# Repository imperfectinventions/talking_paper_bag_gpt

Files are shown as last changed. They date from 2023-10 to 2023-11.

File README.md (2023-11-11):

# Talking Paper Bag GPT

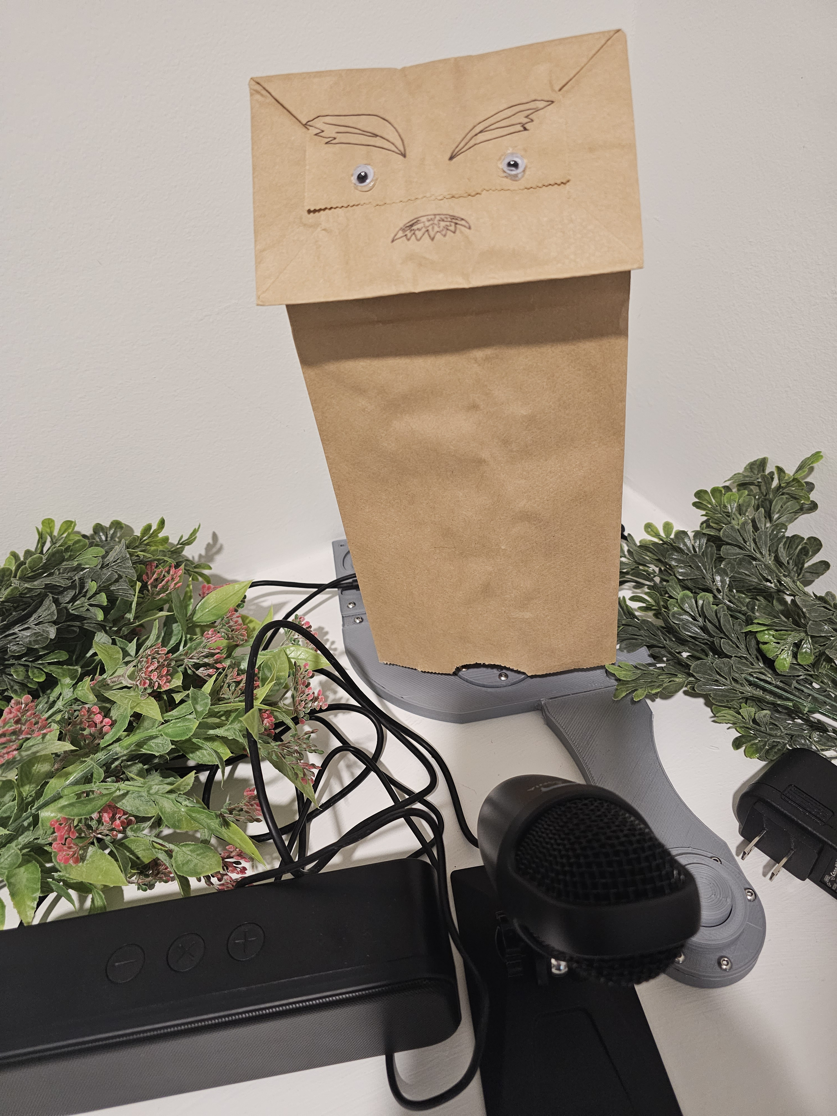
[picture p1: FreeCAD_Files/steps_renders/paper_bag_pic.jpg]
Paper Bag Image


[Demo Link](https://www.instagram.com/p/CzWKE8drE5b/)

# Table of Contents
- [Introduction](#introduction)
- [Requirements](#requirements)
   - [Bill of Materials](#bill-of-materials)
   - [Tools Needed](#tools-needed)
- [Assembly](#assembly)
   - [Print Settings](#print-settings)
   - [Assembly and Setup Steps](#assembly-and-setup-steps)

## Introduction

This device turns any paper bag into a talking puppet! It uses OpenAI's GPT3.5 turbo as well as the Azure Speech service in order to enable communication with this paper bag.

You can also give the paper bag a personality via specifying the system message. I have a few pre-built personalities that you can use (a lot of them are problematic, though so heads up).

## Requirements

### Bill of Materials

|  Name | Purpose | Amazon Link |
|---|---|---|
| 1 Libre AML-S905X-CC | The Brains of the system. Can run linux. Future updates may involve using MicroPython and remove the need for an OS, but this is the current design. Also has 4 USB ports, so it was easy to run USB peripherals on them. | [link](https://www.amazon.com/gp/product/B074P6BNGZ/ref=ppx_yo_dt_b_search_asin_title?ie=UTF8&th=1) |
| 1 SD Card | This will be the non-volatile storage | [link](https://www.amazon.com/SanDisk-Extreme-microSDXC-Memory-Adapter/dp/B09X7BK27V/ref=sr_1_6?keywords=sd+card) |
| 1 Wifi Dongle | WiFi connectivity. This board does have an Ethernet plug so you can use that and free up a USB port. I just went with this. | [link](https://www.amazon.com/gp/product/B0BNFKJPXS/ref=ppx_yo_dt_b_search_asin_title?ie=UTF8&psc=1) |
| Some Stranded Wire | To connect everything together | [Link to the Wire I Used](https://www.amazon.com/gp/product/B077HQ779B/ref=ppx_yo_dt_b_search_asin_title?ie=UTF8&psc=1) |
| Crimp Connectors | To make the wire connections. You could bring your own pre-made wires for this, but I just decided at one point it was cheaper to make my own. | [Link with Crimper](https://www.amazon.com/gp/product/B07VQ6YNSC/ref=ppx_yo_dt_b_search_asin_title?ie=UTF8&psc=1) |
| 1 SG90 Servo | To move the paper bag head. | [Link](https://www.amazon.com/gp/product/B07Q6JGWNV/ref=ppx_yo_dt_b_search_asin_title?ie=UTF8&psc=1) |
| Hot Glue | For glueing things together when needed | [Link](https://www.amazon.com/AdTech-Glue-Sticks-Full-Clear/dp/B000PCY91O/ref=sr_1_4?keywords=glue+gun+sticks) |
| M3 Screws of Various Sizes | For securing all of the 3D printed parts together | [Link](https://www.amazon.com/gp/product/B08H24W42K/ref=ppx_yo_dt_b_search_asin_title?ie=UTF8&psc=1) |
| A USB Speaker | For hearing ChatGPT talk to you. Could go with a combined speaker/microphone.  | [Link](https://www.amazon.com/gp/product/B08QRYTPGH/ref=ppx_yo_dt_b_search_asin_title?ie=UTF8&psc=1) |
| A USB Microphone | For talking to ChatGPT. Could go with a combined speaker/mic. Similar to the one I used. | [Link](https://www.amazon.com/Cyber-Acoustics-Premium-Condenser-Microphone/dp/B0857HD2PT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) |
| PLA Filament | For making the full 3D-printed assembly. | [Link](https://www.amazon.com/gp/product/B08QN5FQX7/ref=ppx_yo_dt_b_search_asin_title?ie=UTF8&psc=1) |
| Some solid core wire | For the button | [Link](https://www.amazon.com/gp/product/B081GMJVPB/ref=ppx_yo_dt_b_search_asin_title?ie=UTF8&psc=1) |
| A Push Button | For controlling when to talk to the Paper Bag | [Link](https://www.amazon.com/gp/product/B09R47N37H/ref=ppx_yo_dt_b_search_asin_title?ie=UTF8&psc=1) |
| Paper Bags | For the whole aesthetic |  | 
| Paper Bag Decorations | For decorations |  |

### Tools Needed

|  Name | Purpose | Amazon Link |
|---|---|---|
| Wire Stripper | Stripping Wires | [Link](https://www.amazon.com/gp/product/B09539R6TD/ref=ppx_yo_dt_b_search_asin_title?ie=UTF8&psc=1) |
| 3D Printer | For printing the full 3D printer assembly | [I use a modded Geeetech A10, but link to some random printer](https://www.amazon.com/Comgrow-Creality-Ender-Aluminum-220x220x250mm/dp/B07BR3F9N6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) | 
| Soldering Iron | For soldering | [Link to Default Soldering Iron, not sponsored](https://www.amazon.com/Soldering-Digital-Welding-Portable-Electric/dp/B08R3515SF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) |
| Hot Glue Gun | For some touch up jobs, securing wires in place, etc. | |

## Assembly

### Print Settings

I printed most parts with 15% infill and surrounded the screw holes and some weak points with 90% infill using a support block in Cura.

### Assembly and Setup Steps

#### Step 1

Step 1

#### Step 2

Step 2

#### Step 3

Step 3

#### Step 4

Step 4

#### Step 5

Step 5

#### Step 6

Step 6

#### Step 7

Step 7

#### Step 8

Step 8

#### Step 9

Step 9

#### Step 10

Step 10

#### Step 11a

Step 11a

#### Step 11b

Step 11b

#### Step 12

Step 12

#### Step 13

Step 13

#### Step 14a

Step 14a

#### Step 14b

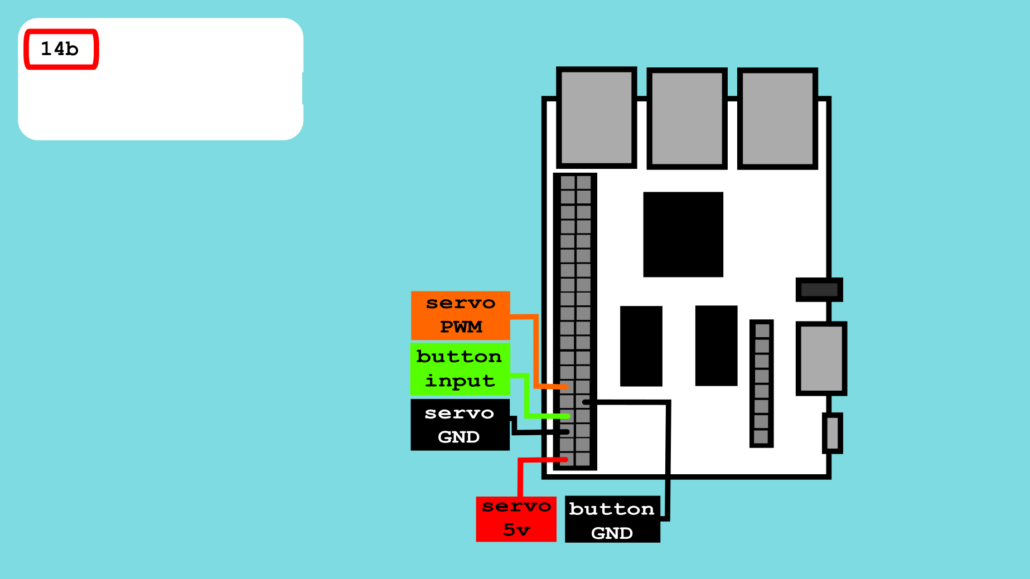
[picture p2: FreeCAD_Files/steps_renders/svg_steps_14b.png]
Step 14b


#### Step 15a

Step 15a

#### Step 15b

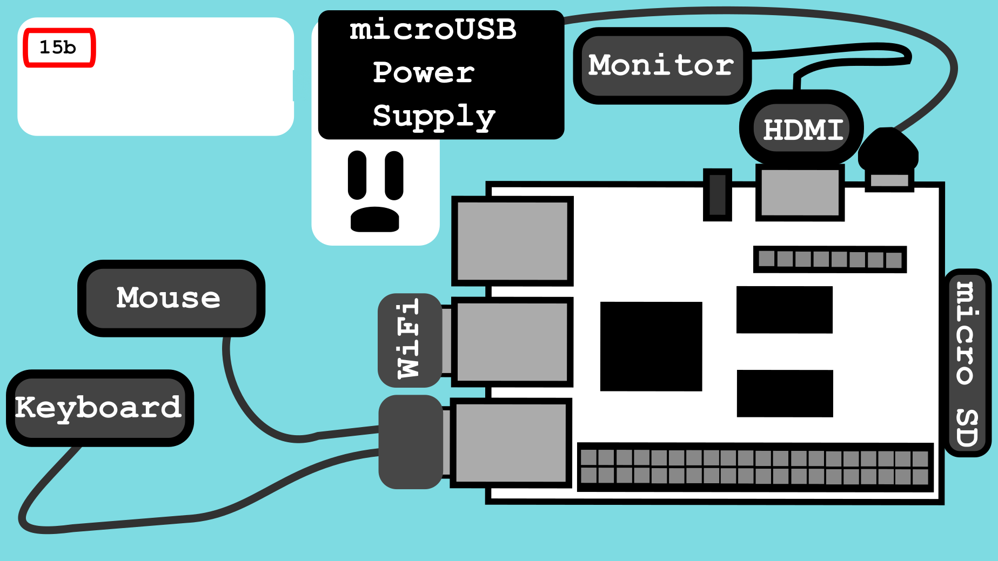
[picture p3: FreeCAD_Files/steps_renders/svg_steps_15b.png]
Step 15b


#### Step 15c: Install the OS

You will now need to set up your micro SD card to hold the OS (or if you go with an eMMC, go with that). The steps for installing Raspbian onto the micro SD is [here](https://hub.libre.computer/t/raspbian-11-bullseye-for-libre-computer-boards/82).

After you install the OS, insert the micro SD into the micro SD slot (shown in step 15a). 

#### Step 15d: Set up your SSH host 

Now that you have a user account set up, make sure to set up your SSH host (just so that you don't need to have a keyboard, mouse, and monitor plugged into the Libre Computer so you can plug in your other devices. NOTE this is only needed if using USB for everything. If you use AV, then you don't necessarily have to do this step).

```bash
sudo apt install openssh-server openssh-client
```

[Reference](https://www.tecmint.com/install-openssh-server-in-linux/)

#### Step 15e: Make sure the Latest Version of Python is Installed

[Follow These Instructions](https://raspberrytips.com/install-latest-python-raspberry-pi/)

#### Step 15f: Install the Necessary Pip Packages (no dokerfile)

If using the dockerfile, skip to [Step 16](#step-16) (recommended you use docker). Follow all the steps normally, then do [Step 22: Docker](#step-22-docker)

With venv
```bash
sudo apt-get install python3-libgpiod #for the gpiod library

python3 -m pip install virtualenv --system-site-packages
python3 -m pip venv pbg-venv
source pbg-venv
pip install -r requirements.txt
```
Witout venv
```bash
pip install -r requirements.txt
```

#### Step 16

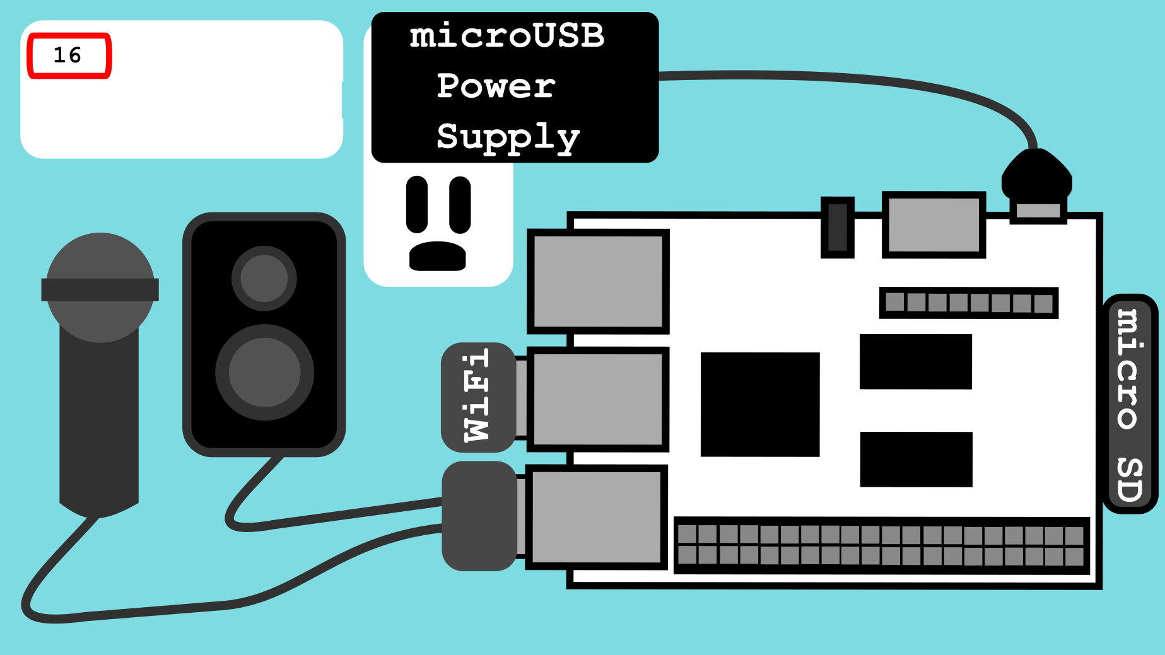
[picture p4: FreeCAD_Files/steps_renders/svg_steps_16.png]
Step 16


#### Step 17: Clone this repo

Clone this repo onto the Libre computer. If you have done this already, kudos. If you have not, do it now.

#### Step 18: Create the cloud resources

[Create a Microsoft Azure Account](https://azure.microsoft.com/en-us/free/)

[Create an Azure subscription or Use an Existing One](https://learn.microsoft.com/en-us/azure/cost-management-billing/manage/create-subscription)
[How to Install and Configure Terraorm for Microsoft Azure](https://learn.microsoft.com/en-us/azure/developer/terraform/quickstart-configure)

Once there is an Azure subscription, terraform is set up, and "az login" or the equivalent command has been run, then it's time to set up the resource groups and the speech/other resources needed.
```bash
#for creating the service account used (make sure to get the account information from this)
cd terraform_code/accounts
terraform init
terraform apply
#for the resource group
cd terraform_code/resource_group
terraform init
terraform apply
```
Then update the settings.yaml file (in the terraform_code directory) with your desired allowed IP addresses that should access your key vault (needs to be the public IP(s) that the Libre Computer is going to connect to). Specify the CIDR and the IP address.

```bash
#for the actual azure resources
cd terraform_code/speech2text
#this terraform will use the settings.yaml file.
terraform init
terraform apply
```

Verify the resources exist:
Look under "resource groups" on portal.azure.com and find the correct resource group known as rg-sbt-ai. Then click on it and make sure the speech resource and the key vault are there
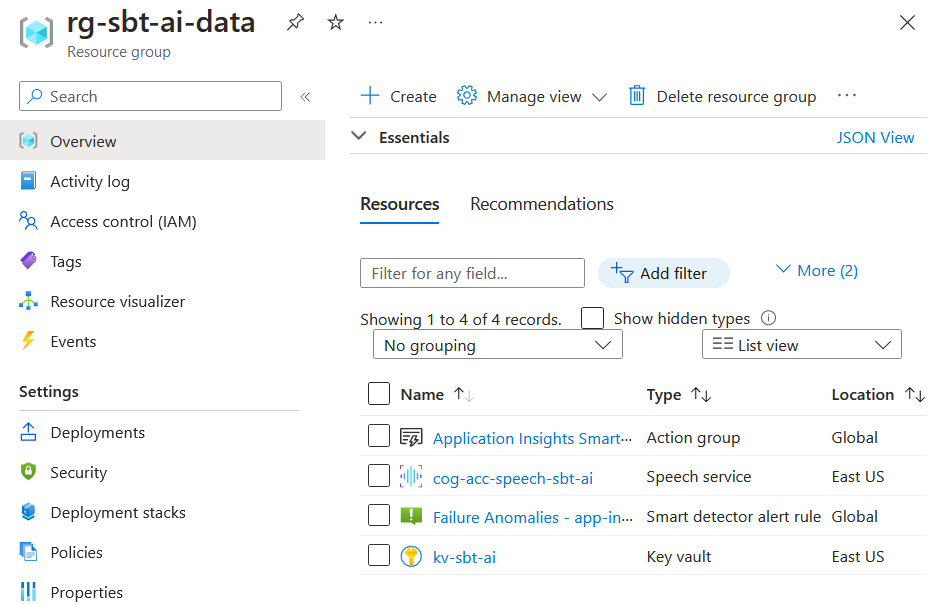
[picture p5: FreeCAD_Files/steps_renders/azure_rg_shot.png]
Look under "resource groups" on portal.azure.com and find the correct resource group known as rg-sbt-ai. Then click on it and make sure the speech resource and the key vault are there


#### Step 19: Get the Azure speech API key

Go to the Azure speech resource named cog-acc-speech-sbt-ai and go down to where it says "KEYS". Use any one of those keys
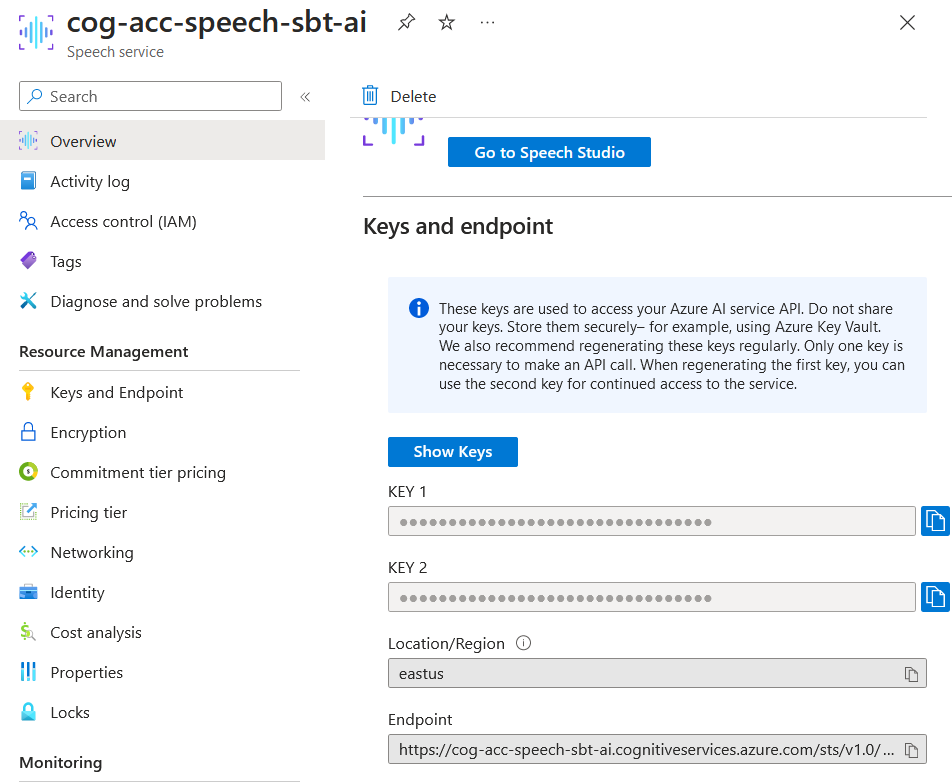
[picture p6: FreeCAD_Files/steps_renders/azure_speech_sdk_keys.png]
Go to the Azure speech resource named cog-acc-speech-sbt-ai and go down to where it says "KEYS". Use any one of those keys


#### Step 20: Get the OpenAI API key

Now got and set up an account with OpenAI. Once done, go to "View API Keys" and "Create a new secret key". This is the key that you will use in step 20 when inserting it into the settings.py file.

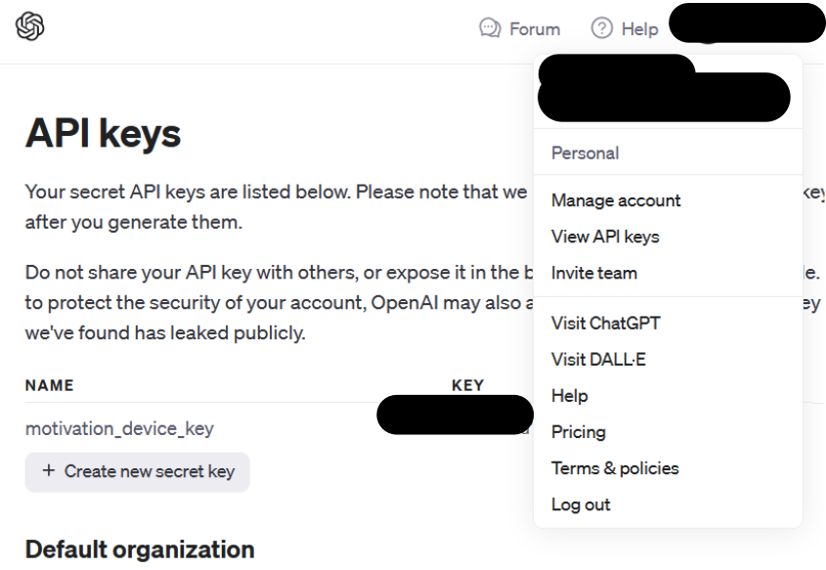
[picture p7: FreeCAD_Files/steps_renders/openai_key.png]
Now got and set up an account with OpenAI. Once done, go to "View API Keys" and "Create a new secret key". This is the key that you will use in step 20 when inserting it into the settings.py file


#### Step 21: Define the settings file

On the Libre Computer clone of this repo in the file named "settings.py", fill out your values. Each value in the settings.py has an explanation where to pull each value from.

#### Step 22: Run it on the Libre Computer! (no docker)

```bash
python main.py
```

#### Step 22: Docker

If running in docker, then:

```bash
#go into the cloned repo's code where the dockerfile is
sudo docker image build -t paper-bag-gpt:0.0.1 .
#run container (need privileged or to map all expected devices/volumes to the container for GPIO and USB)
sudo docker container run --privileged -d paper-bag-gpt:0.0.1 
```
Once docker is up and running, then you should have a working container!

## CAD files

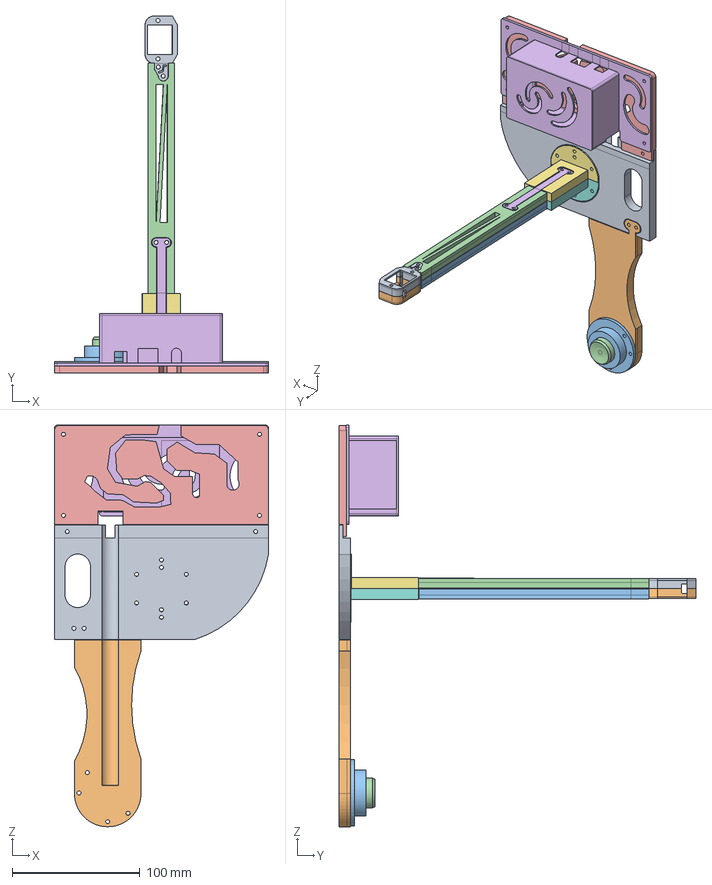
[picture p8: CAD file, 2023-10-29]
FreeCAD_Files/asm_sg90_holder.FCStd
167.4 x 279.2 x 314.0 mm
l_sg90_holder_001
r_sg90_holder_001
r_long_stick_001
l_long_stick_001
stick_key_001
stick_key_002
l_stick_end_001
l_stick_end_002
base_modular_holder_001
button_base_holder_001
button_case_001
button_presser_001
libre_base_001
libre_case_001

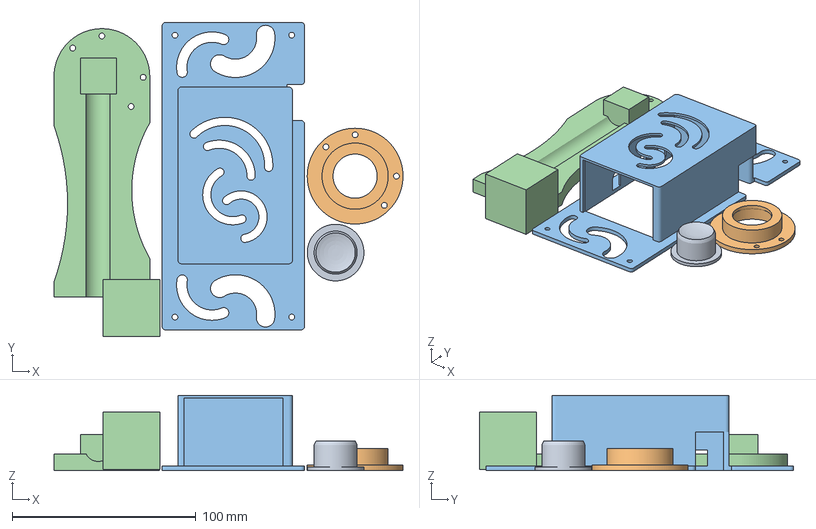
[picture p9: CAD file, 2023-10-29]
FreeCAD_Files/Cura_Multi_Part/button_casing_and_libre_casing.3mf
189.8 x 171.0 x 41.0 mm
button_presser.stl
button_case.stl
libre_case.stl
button_base_holder.stl

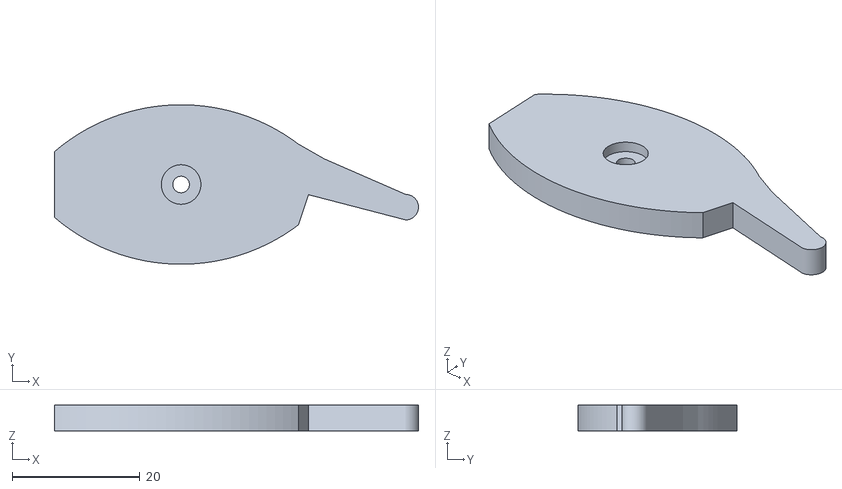
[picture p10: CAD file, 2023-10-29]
FreeCAD_Files/STLs/sg90_move_stick-Body.stl
57.1 x 25.0 x 4.00

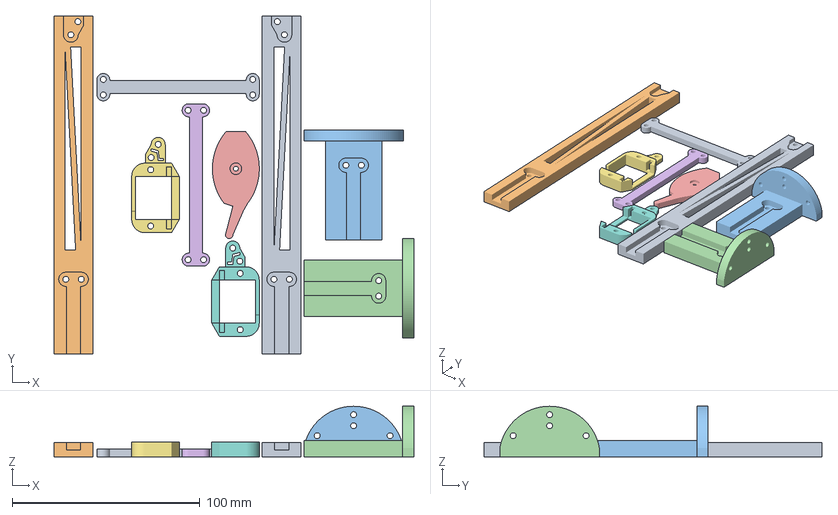
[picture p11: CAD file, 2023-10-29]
FreeCAD_Files/Cura_Multi_Part/sg90_holder_and_tower.3mf
191.7 x 180.0 x 26.9 mm
l_long_stick.stl
r_long_stick.stl
stick_end.stl
stick_end.stl(1)
sg90_move_stick.stl
stick_key.stl
l_sg90_holder.stl
r_sg90_holder.stl
stick_key.stl(1)

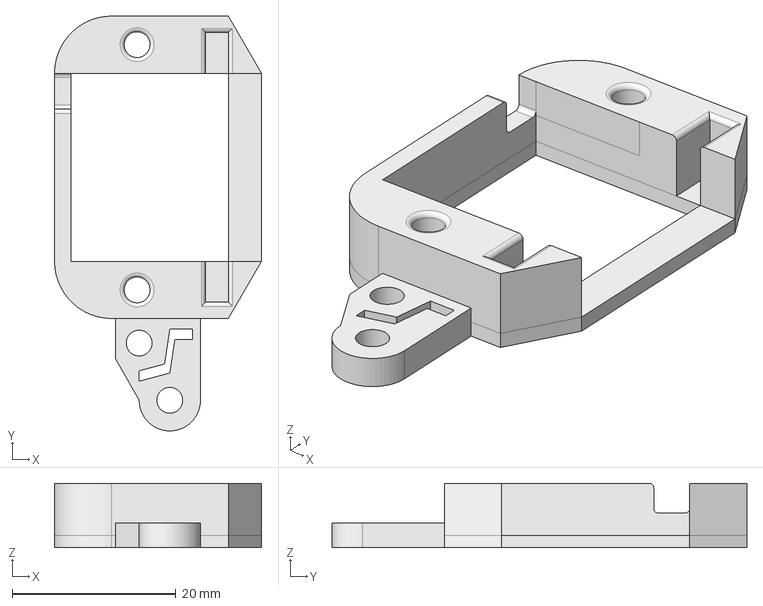
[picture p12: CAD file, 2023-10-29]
FreeCAD_Files/r_sg90_holder.FCStd
25.3 x 50.8 x 7.85 mm

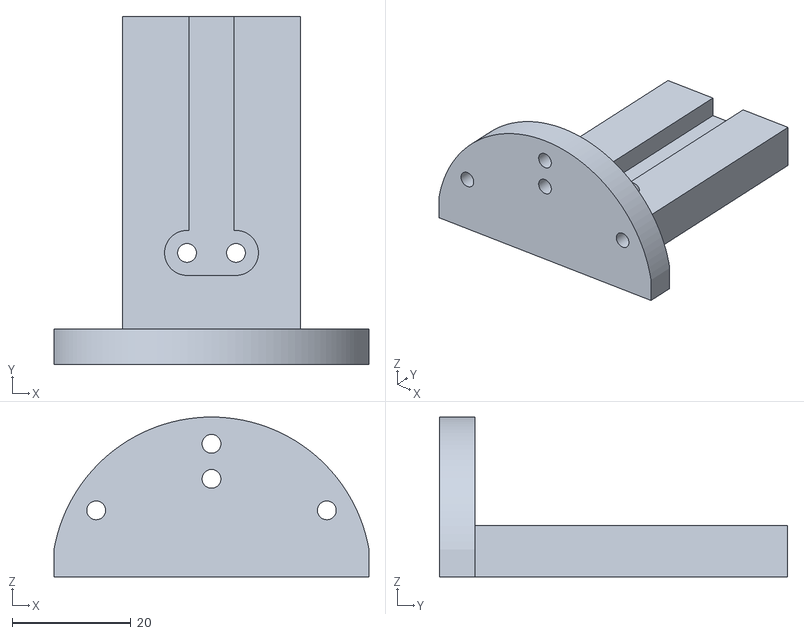
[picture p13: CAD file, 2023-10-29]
FreeCAD_Files/STLs/stick_end.stl
53.0 x 58.6 x 26.9

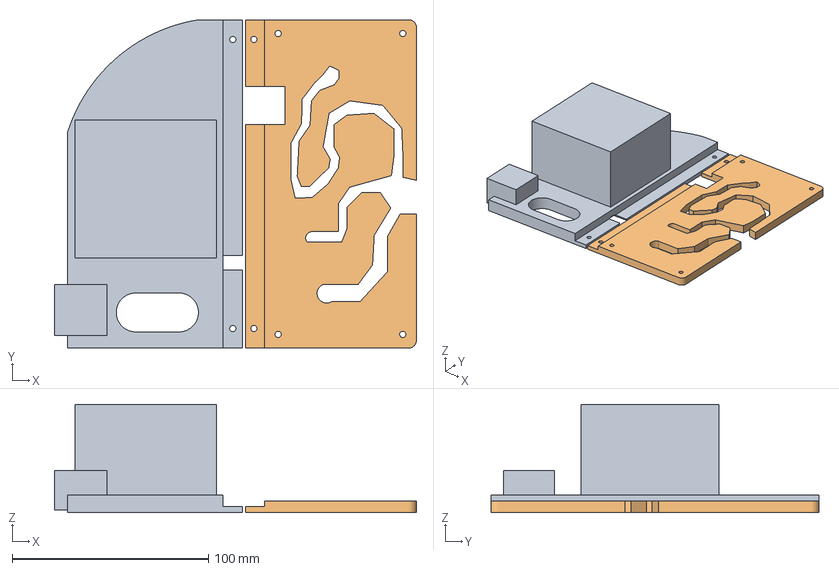
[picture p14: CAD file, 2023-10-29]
FreeCAD_Files/Cura_Multi_Part/sg90_tower_base_libre_base.3mf
184.5 x 167.4 x 55.1 mm
base_modular_holder.stl
libre_base.stl

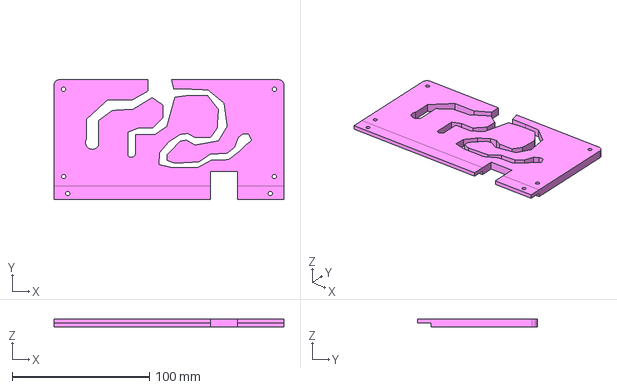
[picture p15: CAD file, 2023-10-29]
FreeCAD_Files/libre_base.FCStd
167.4 x 87.1 x 6.00 mm

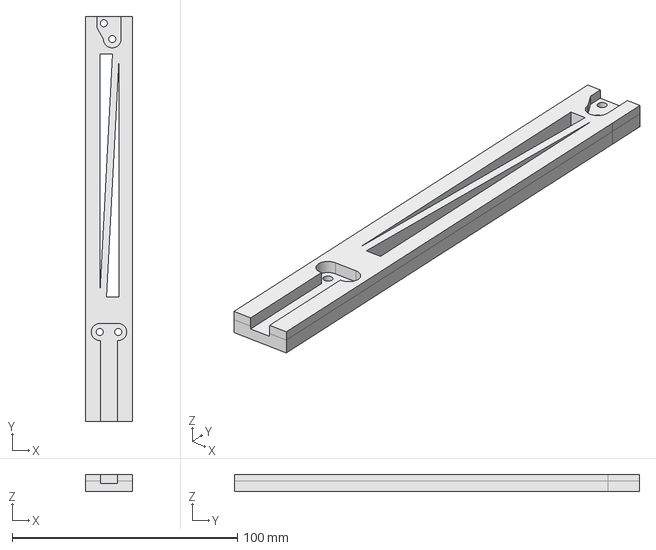
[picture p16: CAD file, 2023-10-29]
FreeCAD_Files/l_long_stick.FCStd
20.8 x 180.0 x 7.65 mm

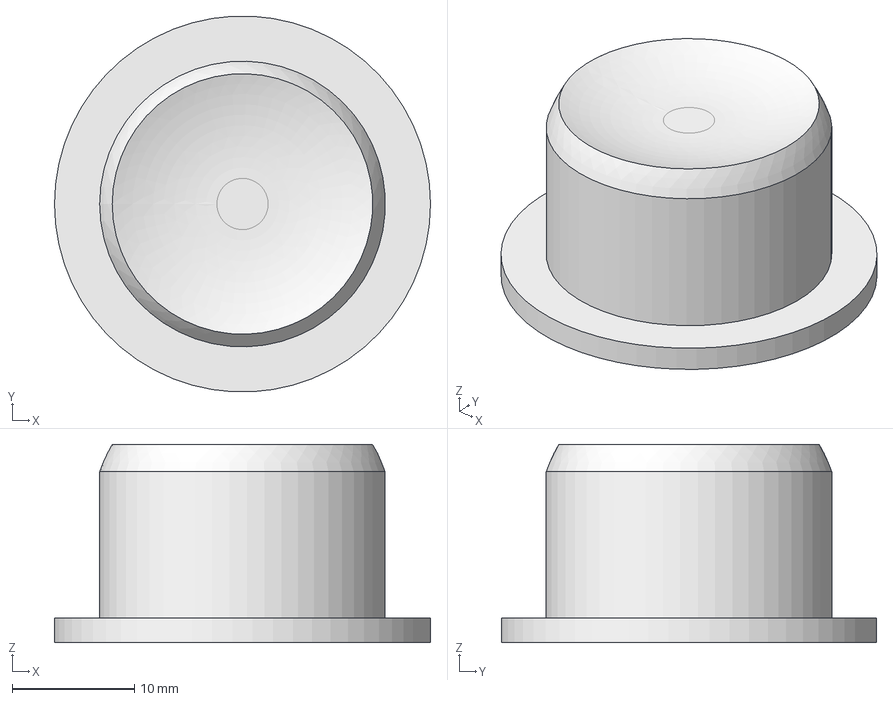
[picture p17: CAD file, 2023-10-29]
FreeCAD_Files/button_presser.FCStd
30.8 x 30.8 x 16.2 mm

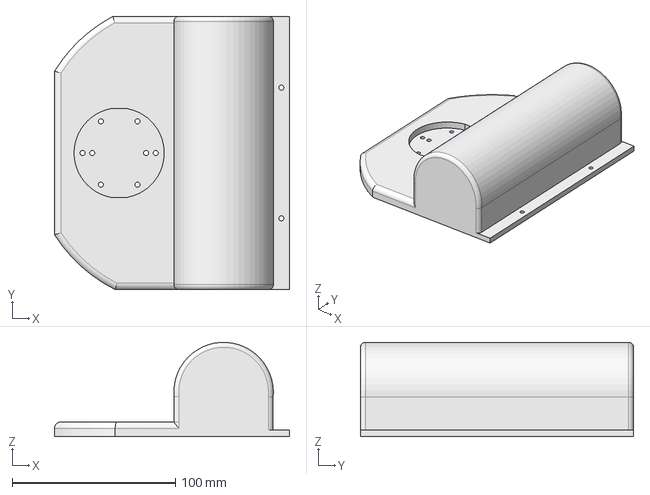
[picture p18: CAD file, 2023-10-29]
FreeCAD_Files/base_weight_holder.FCStd
143.9 x 167.4 x 57.6 mm

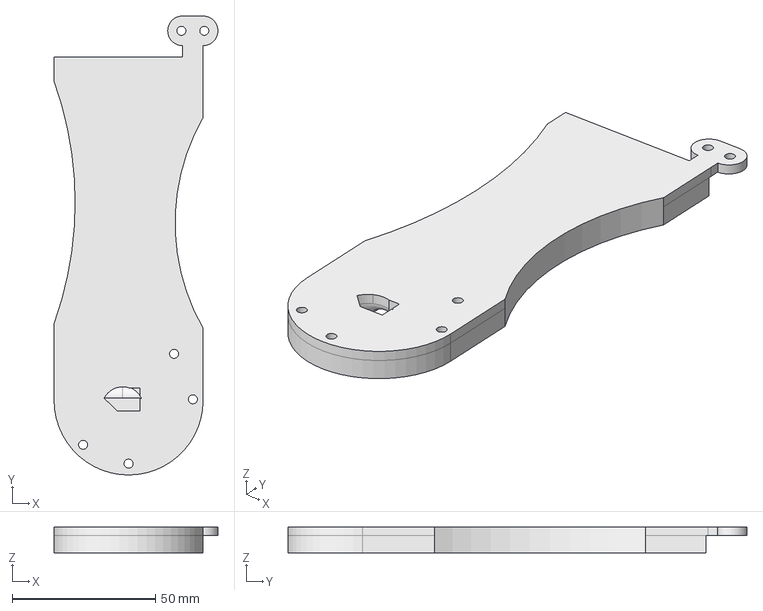
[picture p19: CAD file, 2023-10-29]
FreeCAD_Files/button_base_holder.FCStd
57.3 x 160.4 x 9.00 mm

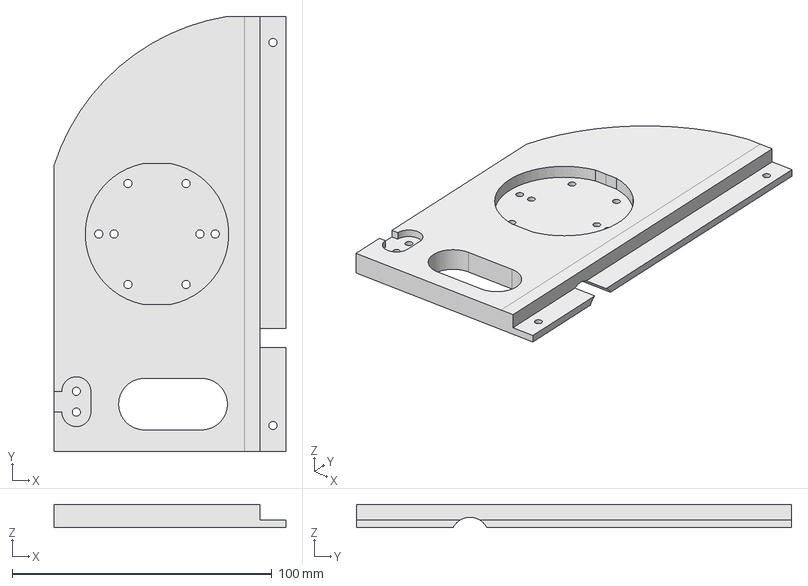
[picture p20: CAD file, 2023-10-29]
FreeCAD_Files/base_modular_holder.FCStd
89.2 x 167.3 x 9.00 mm

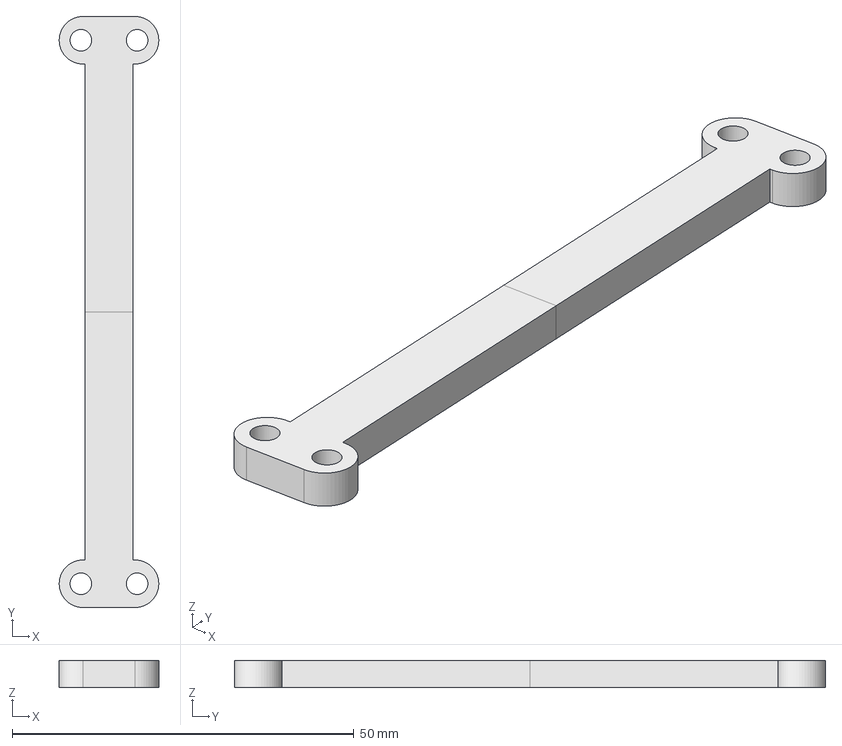
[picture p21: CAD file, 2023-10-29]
FreeCAD_Files/stick_key.FCStd
14.6 x 86.5 x 4.00 mm

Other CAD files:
FreeCAD_Files/l_stick_end.FCStd
FreeCAD_Files/l_sg90_holder.FCStd
FreeCAD_Files/r_long_stick.FCStd
FreeCAD_Files/libre_case.FCStd
FreeCAD_Files/STLs/base_modular_holder.stl
FreeCAD_Files/STLs/button_base_holder.stl
FreeCAD_Files/STLs/button_case.stl
FreeCAD_Files/STLs/button_presser.stl
FreeCAD_Files/STLs/l_long_stick.stl
FreeCAD_Files/STLs/l_sg90_holder.stl
FreeCAD_Files/STLs/libre_base.stl
FreeCAD_Files/STLs/libre_case.stl
FreeCAD_Files/STLs/r_long_stick.stl
FreeCAD_Files/STLs/r_sg90_holder.stl
FreeCAD_Files/STLs/sg90_move_stick.stl
FreeCAD_Files/STLs/stick_key.stl
FreeCAD_Files/button_case.FCStd
FreeCAD_Files/libre_base (1).FCStd
FreeCAD_Files/libre_case (1).FCStd
FreeCAD_Files/sg90_move_stick.FCStd

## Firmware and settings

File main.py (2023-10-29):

import random
import openai
import datetime
import time
import json
import gpiod
import sys
import azure.cognitiveservices.speech as speechsdk
import settings
from periphery import PWM
import subprocess
import numpy
import threading
import tiktoken

#CHANGE THESE ONCE WORKING
viseme_event_now = False
viseme_num = 0
kill_viseme = False

#need to run this with root privilege because of ldto enable/disable
def activate_pwm(pwm_name, pwm_chip_num):
    #you can get the pwm chip numbers in ldto list and:
    # https://hub.libre.computer/t/how-to-enable-and-control-pwm-on-aml-s905x-cc/243
    already_active = False
    for i in subprocess.getoutput('ldto status').split('\n'):
        if i == pwm_name:
            print(f"PWM name: {pwm_name} already set")
            already_active = True
    if not already_active:
        print(f"PWM name: {pwm_name} setting...")
        subprocess.getoutput(f'sudo ldto enable {pwm_name}')
        subprocess.getoutput(f'sudo echo 1 > /sys/class/pwm/pwmchip{pwm_chip_num}/export')
        #set export to be writable by all so that PWM will succeed on the first time. Not fully sure why permission denied the first time, then succeeds second time. FIXME
        subprocess.getoutput(f'sudo chmod 222 /sys/class/pwm/pwmchip{pwm_chip_num}/export')

def deactivate_pwm(pwm_name):
    already_active = False
    for i in subprocess.getoutput('ldto status').split('\n'):
        if i == pwm_name:
            print(f"PWM name: {pwm_name} set")
            already_active = True
    if already_active:
        print(f"PWM name: {pwm_name} disabling...")
        subprocess.getoutput(f'sudo ldto disable {pwm_name}')
    else:
        print(f"PWM name: {pwm_name} already not active")
class pwm_runner:
    def __init__(self, chip_num, channel_num, secs_per_deg = (0.1/60), period_ns=2400000, duty_cycle_ns=400000, step_ns=100000):
        self.chip_num = chip_num
        self.channel_num = channel_num
        self.secs_per_deg = secs_per_deg
        self.period_ns = period_ns
        self.duty_cycle_ns = duty_cycle_ns
        self.step_ns = step_ns
        self.__pwm_obj = PWM(chip_num, channel_num)
        self.__pwm_obj.period_ns = period_ns
        self.__pwm_obj.duty_cycle_ns = period_ns
        self.__pwm_obj.enable()
    def __enter__(self):
        return self
    def __exit__(self, exc_type, exc_value, traceback):
        self.__pwm_obj.close()

    def set_pos(self, angle):
        self.__pwm_obj.duty_cycle_ns = int(self.duty_cycle_ns + (self.period_ns - self.duty_cycle_ns)* (int(angle)/180))

    def close(self):
        self.__pwm_obj.close()

def push_button_record(button_pin_num, button_chip_num):
    curr_text_index = 0
    finalized_text = ['']
    audio_config = speechsdk.AudioConfig(device_name=settings.mic_device_name)
    speech_config = speechsdk.SpeechConfig(subscription=settings.azure_sub, region=settings.azure_region)
    speech_recognizer = speechsdk.SpeechRecognizer(speech_config=speech_config, audio_config=audio_config)
    done = False

    def recognizing_cb(evt: speechsdk.SpeechRecognitionEventArgs):
        nonlocal finalized_text
        nonlocal curr_text_index
        if len(finalized_text) < curr_text_index + 1:
            finalized_text.append('')
        finalized_text[curr_text_index] = str(evt.result.text)

    def recognized_cb(evt: speechsdk.SpeechRecognitionEventArgs):
        nonlocal finalized_text
        nonlocal curr_text_index
        if len(finalized_text) < curr_text_index + 1:
            finalized_text.append('')
        finalized_text[curr_text_index] = str(evt.result.text)
        print(finalized_text[curr_text_index])
        curr_text_index += 1

    def stop_cb(evt: speechsdk.SessionEventArgs):
        """callback that signals to stop continuous recognition"""
        nonlocal done
        done = True

    # Connect callbacks to the events fired by the speech recognizer
    speech_recognizer.recognizing.connect(recognizing_cb)
    speech_recognizer.recognized.connect(recognized_cb)
    speech_recognizer.session_stopped.connect(stop_cb)
    speech_recognizer.canceled.connect(stop_cb)

    with gpiod.Chip('gpiochip'+str(button_chip_num)) as chip:
      lines = chip.get_line(button_pin_num)
      lines.request(consumer=sys.argv[0], type=gpiod.LINE_REQ_DIR_IN, flags=gpiod.LINE_REQ_FLAG_BIAS_PULL_UP | gpiod.LINE_REQ_FLAG_ACTIVE_LOW)
      last_time = time.time()*1000
      operation = 'noop'
      kicked_off = False
      while True:
        curr_time = time.time()*1000
        time_diff = curr_time - last_time
        if time_diff >= 50:
          val = lines.get_value()
          if val > 0:
            operation = 'rec'
          else:
            operation = 'noop'
        curr_speech_pointer = None
        if operation == 'rec':
            if not kicked_off:
                curr_speech_pointer = speech_recognizer.start_continuous_recognition_async()
                curr_speech_pointer.get()
                kicked_off = True
        else:
            if kicked_off:
                speech_recognizer.stop_continuous_recognition_async()
                kicked_off = False
                while not done:
                    pass
                combined_text = ""
                for i in finalized_text:
                    combined_text = combined_text + " " + i 
                return combined_text

def gen_system_content(convo_dict, system_start_file):
    speech_guide_file = open(system_start_file, "r")
    file_read_data = speech_guide_file.read()
    convo_dict["curr_convo"].append({ "role" : "system", "content" : file_read_data })
    curr_enc = tiktoken.encoding_for_model(convo_dict["model"])
    convo_dict["curr_token_count"] += len(curr_enc.encode(file_read_data)) + 10 #10 is magic for now
    #convo_dict["raw_text"] += file_read_data

def gen_assistant_content(convo_dict, assistant_response):
    convo_dict["curr_convo"].append({ "role" : "assistant", "content" : assistant_response })
    convo_dict["raw_text"] += " " + assistant_response
    curr_enc = tiktoken.encoding_for_model(convo_dict["model"])
    convo_dict["curr_token_count"] += len(curr_enc.encode(assistant_response)) + 10 #10 is magic


def gen_user_response(convo_dict, user_response):
    convo_dict["curr_convo"].append({ "role" : "user", "content" : user_response })
    convo_dict["raw_text"] += " " + user_response
    curr_enc = tiktoken.encoding_for_model(convo_dict["model"])
    convo_dict["curr_token_count"] += len(curr_enc.encode(user_response)) + 5 #5 is magic for internal tokesn used

def visemes2servo(*pwm_run):
    #pass in low as 0 high as 1 and pwm_runner as 2
    low = pwm_run[0]
    high = pwm_run[1]
    secs_per_deg = (0.1/60)
    last_setting = False
    global kill_viseme
    global viseme_event_now
    global viseme_num
    open_mouths = [1, 2, 9, 11, 20]
    closed_mouths = [0, 18, 21 ]
    oooo_mouths = [3, 7, 10, 13]
    mid_mouths = [4, 5, 8, 12, 14, 17, 19 ]
    mid_low_mouths = [6, 15, 16 ]
    last_angle = 0
    curr_angle = 0
    while not kill_viseme:
        if viseme_event_now: 
            if viseme_num in open_mouths:
                pwm_run[2].set_pos(high)
                curr_angle = high
            elif viseme_num in oooo_mouths or viseme_num in mid_mouths:
                pwm_run[2].set_pos(low + (high-low)//2)
                curr_angle = low + (high-low)//2
            elif viseme_num in mid_low_mouths: 
                pwm_run[2].set_pos(low + (high-low)//4)
                curr_angle = low + (high-low)//4
            else: 
                pwm_run[2].set_pos(low)
                curr_angle = low 
            time.sleep(int(abs(curr_angle-last_angle)*secs_per_deg))
            last_angle = curr_angle
            viseme_event_now = False
    return last_setting

def gpt35_summ_gen(*thread_args):
        print("Summarizing... Hit", thread_args[0]["curr_token_count"])
        curr_enc = tiktoken.encoding_for_model(thread_args[0]["model"])
        sys_msg = "You are an expert at summarizing conversations. Your summarizations still sound like someone is recounting a memory. Your conversation summarization will be used to continue conversations"
        user_msg = "Please summarize our past conversation. Disregard system messages and your previous conversation. Just summarize what you said within 40-70 words so that we can continue our conversation. Here is the conversation:" + thread_args[0]["raw_text"]
        old_convo = thread_args[0]["curr_convo"][0].copy()
        curr_token_size = curr_enc.encode(sys_msg + " " + user_msg)
        thread_args[0]["curr_convo"] = [{ "role" : "system", "content" : sys_msg}]
        thread_args[0]["raw_text"] = ""
        gen_user_response(thread_args[0], user_msg)
        response = openai.ChatCompletion.create(
            model=thread_args[0]["model"],
            messages=thread_args[0]["curr_convo"],
            temperature=thread_args[0]["temperature"],
            max_tokens=thread_args[0]["max_tokens"] - len(curr_token_size) - 10 - 5,
        )
        gen_assistant_content(thread_args[0], response.choices[0].message.content) 
        thread_args[0]["curr_convo"] = [old_convo, thread_args[0]["curr_convo"][len(thread_args[0]["curr_convo"]) -1 ]] 
        thread_args[0]["raw_text"] = response.choices[0].message.content
        curr_enc = tiktoken.encoding_for_model(thread_args[0]["model"])
        thread_args[0]["curr_token_count"] = response.usage.total_tokens 
        return response.choices[0].message.content

def gpt35_convo_gen(convo_dict):
        curr_enc = tiktoken.encoding_for_model(convo_dict["model"])
        response = openai.ChatCompletion.create(
            model=convo_dict["model"],
            messages=convo_dict["curr_convo"],
            temperature=convo_dict["temperature"],
            max_tokens=convo_dict["max_tokens"] - convo_dict["curr_token_count"], 
        )
        print(response.choices[0].message.content)
        convo_dict["curr_token_count"] = response.usage.total_tokens
        gen_assistant_content(convo_dict, response.choices[0].message.content)
        return response.choices[0].message.content

def text2speech(pwm_obj, openai_text, voice_name="en-US-GuyNeural"):
    last_time = time.time()
    last_setting = False
    def phenome_rec_audio_event(evt: speechsdk.SpeechSynthesisVisemeEventArgs):
        global viseme_event_now
        global viseme_num
        viseme_event_now = True
        viseme_num = evt.viseme_id
    audio_complete = False
    def complete_audio_event(evt: speechsdk.SpeechRecognitionEventArgs):
        nonlocal audio_complete
        audio_complete = True
        print("Synthesis completed: {}".format(evt))
    speech_config = speechsdk.SpeechConfig(subscription=settings.azure_sub, region=settings.azure_region)

    # Set the voice name, refer to https://aka.ms/speech/voices/neural for full list.
    speech_config.speech_synthesis_voice_name = voice_name
    stream_config = speechsdk.audio.AudioOutputConfig(device_name=settings.speaker_device_name)
    speech_synthesizer = speechsdk.SpeechSynthesizer(speech_config=speech_config, audio_config=stream_config)
    
    speech_synthesizer.viseme_received.connect(phenome_rec_audio_event)
    speech_synthesizer.synthesis_completed.connect(complete_audio_event)

    result = speech_synthesizer.speak_text_async(openai_text).get()


if __name__ == "__main__":
    openai.api_key = settings.openai_key 
    convo_dict = {
                    "model" : "gpt-3.5-turbo",
                    "temperature" : 1.25,
                    "max_tokens" : 3800, 
                    "curr_token_count" : 0,
                    "summarize_token_time" : 2000, 
                    "curr_convo" : [], 
                    "raw_text" : ""}
    activate_pwm(settings.pwm_pin_name, settings.pwm_chip_num)
    pwm_obj = pwm_runner(settings.pwm_chip_num, settings.pwm_channel_num)
    servo_thread = threading.Thread(target=visemes2servo, args=(settings.servo_angles[0], settings.servo_angles[1], pwm_obj,))
    servo_thread.start()
    gen_system_content(convo_dict, settings.system_conf_prompt)
    gen_assistant_content(convo_dict, settings.system_start_talk)
    text2speech(pwm_obj, settings.system_start_talk, voice_name=settings.speech_voice_name)
    if settings.mode == "reddit":
        reddit_file = open(settings.reddit_story, 'r+')
        gen_user_response(convo_dict, "I need your moral judgement on this Reddit story: " + reddit_file.read())
        reddit_file.close()
        curr_msg = gpt35_convo_gen(convo_dict)
        print("I've got this juicy goss...")
        with gpiod.Chip('gpiochip'+str(settings.button_chip_num)) as chip:
            lines = chip.get_line(settings.button_pin_num)
            lines.request(consumer=sys.argv[0], type=gpiod.LINE_REQ_DIR_IN, flags=gpiod.LINE_REQ_FLAG_BIAS_PULL_UP | gpiod.LINE_REQ_FLAG_ACTIVE_LOW)
            while lines.get_value() == 0:
                pass
            text2speech(pwm_obj, curr_msg, voice_name=settings.speech_voice_name)
        print("Done first tts gen")
    print(settings.system_start_talk)

    
    summ_thread = None
    new_convo_dict = None
    count_since_thread_ran = 1
    tokens_since_thread_ran = 0
    while True:
        curr_thread_count = convo_dict["curr_token_count"]
        if not summ_thread and convo_dict["curr_token_count"] >= convo_dict["summarize_token_time"]:
            count_since_thread_ran = 1
            tokens_since_thread_ran = 0
            new_convo_dict = convo_dict.copy()
            summ_thread = threading.Thread(target=gpt35_summ_gen, args=(new_convo_dict,))
            summ_thread.start()
        store_human_speech = push_button_record(settings.button_pin_num, settings.button_chip_num)
        print(store_human_speech)
        gen_user_response(convo_dict, store_human_speech) 
        curr_msg = gpt35_convo_gen(convo_dict)
        text2speech(pwm_obj, curr_msg, voice_name=settings.speech_voice_name)
        if summ_thread and not summ_thread.is_alive():
           summ_thread = None
           convo_appends = []
           for i in range(len(convo_dict["curr_convo"]) - count_since_thread_ran*2 - 1, len(convo_dict["curr_convo"])-1):
                convo_appends.append(convo_dict["curr_convo"][i])
           new_convo_dict["curr_convo"] + convo_appends
           count_since_thread_ran = 1
           convo_dict = new_convo_dict
        else:
            tokens_since_thread_ran += convo_dict["curr_token_count"] - curr_thread_count
            count_since_thread_ran += 1
        last_token_count = convo_dict["curr_token_count"]
            
    kill_viseme = True
    servo_thread.join()
    pwm_obj.close()
    deactivate_pwm()

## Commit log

2023-08-20 Initial setup for end to end speech that is right now pretty quick, but not set up for multi processing/threading. Need to move in that direction
2023-09-20 Try adding event in for continue to process. Causes servo freakout right now.
2023-09-22 Working using threads and visemes where the paper bag only responds when it isn't moving
2023-09-24 Add basis for a thread to run and grab the summarized information while talking
2023-10-01 Added cluge to PWM init setup so that will allow all to write to PWMCHIP0. Not ideal for multiple user systems (but this one is just one user right now, so)
2023-10-03 Update README.md and add BOM and table of contents
2023-10-03 Cleanup code, reorganize, and replace
    [main.py]
2023-10-15 Upload FreeCAD files
    [asm_sg90_holder.FCStd, base_modular_holder.FCStd, base_weight_holder.FCStd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]
2023-10-15 Update to include .FCStd1
    [libre_base.FCStd, libre_case.FCStd, stick_key.FCStd]
2023-10-15 Add assembly Cura files and stls
    [asm_sg90_holder.FCStd, base_modular_holder.FCStd, base_modular_holder.stl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]
2023-10-18 Update the move stick to be better spaced out
    [sg90_move_stick.FCStd, sg90_move_stick.stl]
2023-10-29 Add renders and SVG for the docs
    [asm_sg90_holder.FCStd]
2023-10-29 Add lego-style assembly steps (does have oversaturation problem)
